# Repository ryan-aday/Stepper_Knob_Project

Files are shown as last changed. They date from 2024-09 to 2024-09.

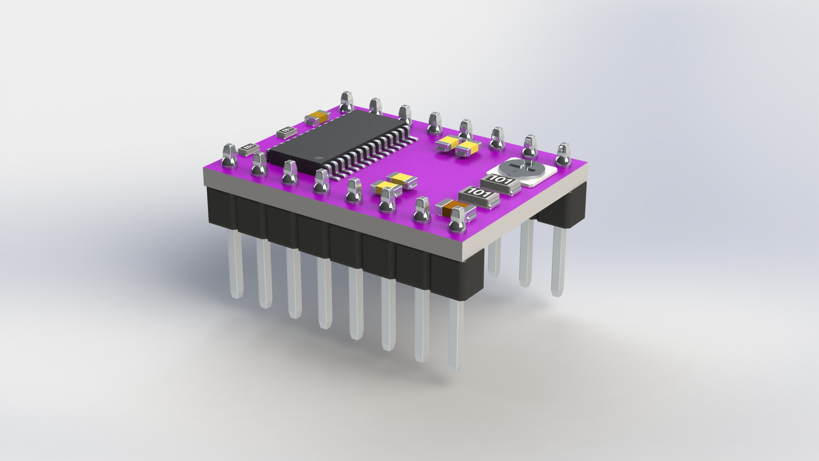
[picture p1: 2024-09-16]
Assem_PCB_Mockup/stepper-motor-driver-drv8825-1.snapshot.2/Stepper Motor Driver DRV8825 3DView.JPG

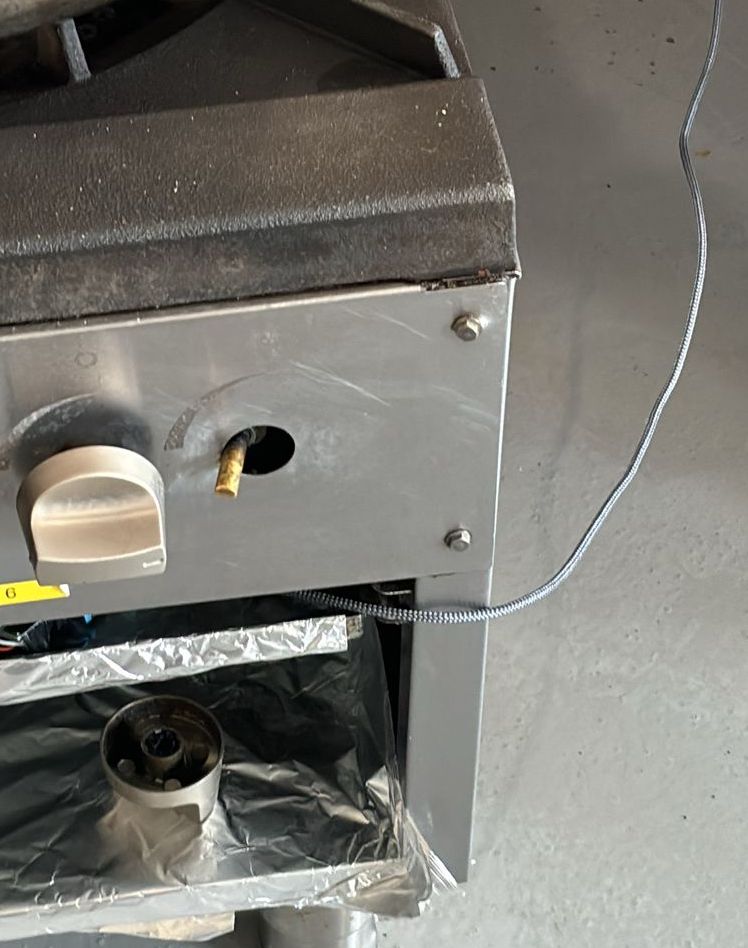
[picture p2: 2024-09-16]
Documentation/SampleGasKnobs/SampleGasKnobs/SlantedPin.jpg

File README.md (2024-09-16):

# Stepper_Knob
Hardware, firmware development of an automatable kitchen knob.



## Documentation

The CAD files have been drawn up in Solidworks 2024.

The main assembly to view is Knob_Assembly_SM.sldasm.

CAD files made by me are for the potentiometer, stepper motor, knob, and chassis.

Full size chassis drawings may be found in the Documentation folder and the Summary Sheet.

Other parts drawings may be found in the BOM references.

The summary sheet can be opened with LibreOffice and its equivalents.

The stepper schematic can be opened with Fritzing (v.1.0.3 recommended as of 09/16/2024). https://fritzing.org/

### Chassis Sheet Metal Flat Drawing


### Chassis Sheet Metal Flat Drawing


### Wiring Diagram
Wiring_Diag_Breadboard

### Wiring Schematic
Wiring_Diag_Schem

### PCB Mockup
PCB_Prototype

### BOM
See Documentation -> Summary Sheet -> BOM.
Total material cost is ~$150.29 sans shipping, wiring, and manufacturing costs.

| Part | Description | Vendor | Number | Unit Price | Total Cost | Link(s) |
|:---|:---|:---|---:|:---|:---|:---|
| HT17-222_RevD | Double Sided Double Pole 0.9 Deg Step Stepper Motor | Applied Motion Products | 1 | $56.00 | $56.00 | https://applied-motion.s3.amazonaws.com/documents/2D-Drawing/HT17-222_RevD.pdf https://www.applied-motion.com/s/product/step-motor-9-degreeht17222d/01t5i000000y0ElAAI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 |
| 5mm Vertical Slide Switch | Slide Switch | uxCell | 1 | $0.51 | $0.51 | https://www.amazon.com/uxcell-Vertical-Switch-Terminals-Latching/dp/B07GSJHGD2 |
| ESP32 WROOM RevE | Microcontroller | Esspressif | 1 | $10.00 | $10.00 | https://www.digikey.com/en/products/detail/espressif-systems/ESP32-DEVKITC-32E/12091810 https://www.digikey.com/en/models/9356990 https://forum.fritzing.org/t/esp32-wroom-32u/12978 https://grabcad.com/library/esp32-19 |
| 10k Ohm Through Hole Resistor  | Standard throughhole resistor | Adafruit | 1 | $0.03 | $0.03 | https://grabcad.com/library/resistors-0-5w-pitch-10-2mm-401-57mil-1 https://www.adafruit.com/product/2784 |
| DRV8833 | Stepper motor controller | Adafruit | 1 | $5.95 | $5.95 | https://www.adafruit.com/product/3297#technical-details https://github.com/adafruit/Fritzing-Library https://grabcad.com/library/stepper-motor-driver-drv8825-1 |
| 5mm Universal Joint | Universal Joint | Befenybay | 1 | $2.75 | $2.75 | https://www.amazon.com/Befenybay-Universal-Joint-Coupling-Screws/dp/B07VC9F1RH |
| RH24PC | Potentiometer | P3 America | 1 | $16.00 | $16.00 | https://p3america.com/rh24pc-110mm-series/ |
| NXFT15XH103FA2B090 | Thermistor | NXF | 1 | $0.48 | $0.48 | https://grabcad.com/library/thermistor-nxft15xh103fa2b090-1 https://www.digikey.com/en/products/detail/murata-electronics/NXFT15XH103FA2B090/5797782 |
| 9262K623 | Oil Resistant O-Ring 1mm wide 24mm ID | McMaster-Carr | 1 | $0.13 | $0.13 | https://www.mcmaster.com/9262K623/ |
| 90591A109 | Zinc-Plated Steel Nut M1.6x035mm | McMaster-Carr | 2 | $0.23 | $0.46 | https://www.mcmaster.com/90591A109/ |
| 91292A265 | 18-8 Stainless Steel Socket Head Screw M1.6x0.35 10mm long | McMaster-Carr | 2 | $0.27 | $0.53 | https://www.mcmaster.com/91292A265/ |
| 92095A119 | Button Head Hex Drive Head Screw 18-8 SS M3x0.5 15 long | McMaster-Carr | 4 | $0.06 | $0.25 | https://www.mcmaster.com/92095A119/ |
| 92095A183 | Button Head Hex Drive Screw 18-8 SS M3x0.5mm 12mm long | McMaster-Carr | 3 | $0.07 | $0.20 | https://www.mcmaster.com/92095A183/ |
| 92095A451 | Button Head Hex Drive Screw M2x0.04mm 4mm long 18-8 SS M3x0.5mm 12mm long | McMaster-Carr | 2 | $0.18 | $0.36 | https://www.mcmaster.com/92095A451/ |
| 92470A144 | Phillips Rounded Head Screw 18-8 SS No. 6 ¼” long | McMaster-Carr | 2 | $0.07 | $0.13 | https://www.mcmaster.com/92470A144/ |
| U Joint Cover | U Joint Sock (Provided Example) | McMaster-Carr | 1 | $10.00 | $10.00 | https://woodmaxx.com/product/u-joint-rubber-boot-cover/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 |
| 94000A330 | 18-8 Stainless Steel Cap Screw Nut M3x0.5mm | McMaster-Carr | 3 | $0.47 | $1.40 | https://www.mcmaster.com/94000A330/ |
| 94868A718 | Female Thread Hex Standoff 18-8 SS 4.5mm Hex 7mm Long M3x0.5mm | McMaster-Carr | 3 | $4.08 | $12.24 | https://www.mcmaster.com/94868A718/ |
| 8983K135 | SS 304 Sheet 12”x12” 0.06” thick | McMaster-Carr | 1 | $32.85 | $32.85 | https://www.mcmaster.com/8983K42/ |

### Code
See Documentation -> Stepper_Knob_Code.

This code controls a stepper motor using an ESP32, WiFi, and Bluetooth Low Energy (BLE) communication. It includes features for reading a thermistor, potentiometer, and handling motor control.
  - WiFi and BLE: It initializes WiFi and BLE to allow remote monitoring and control of the motor's position. The current potentiometer angle is transmitted via BLE notifications.
  - Stepper Motor Control: The code controls a stepper motor using a DRV8833 motor driver. It steps the motor based on the angle read from a potentiometer and allows for switching between "Free" and "Automated" modes via a toggle switch:
      - Free Mode: The motor is disabled, but the potentiometer angle is still read.
      - Automated Mode: The motor moves to match the potentiometer's position.
  - Thermistor: A thermistor is used to monitor temperature. If the temperature exceeds a set threshold (70°C), the motor is disabled to prevent thermal runaway.
  - Potentiometer: The potentiometer's analog reading is mapped to a specific angle (0 to 340 degrees) and used to control the stepper motor’s position.
  - Motor Step Calculation: The motor is stepped based on the target angle, which is calculated from the potentiometer reading. The motor control logic handles the necessary steps to rotate the motor.

This setup allows remote control and monitoring of the motor's behavior while incorporating safety measures against overheating.

### Design Philosophy Explanations
See Documentation -> Summary Sheet -> Justification.

| Feature | Description |
|---|---|
| **General Design** | Reduced volume/area taken by knob. Integrated PCB and assembly, allowing space for future proofing. |
| **Dual shaft stepper** | Less torque, but less power requirements. UL1061 wiring sufficient for 80 deg temperatures. |
| **Motor Controller** | Cheap, low voltage/power. Has built-in Wifi & BLE capability. |
| **U-Joint** | Ensures rotational accuracy, single joint for cost and space. Joint protected by a neoprene sock for chemical and heat protection. |
| **PCB Design** | Minimized hand wiring for assembly, including the switch. Used dev board for prototyping with extra ports for additional features. |
| **Thermistor** | Added for thermal runaway shutoff protection. |
| **Power** | 5V microUSB rail, also serves as a bootstrap port. Enclosed to avoid hacking, but inline with available stove source gaps. |
| **PCB Wiring** | Can be routed through a hole into the mounting space. |
| **Sheet Metal Chassis** | Cheaper for mass production, leveraging material tolerances. |
| **Sheet Metal Material & Wall Thickness** | Stainless 304 for cheap SS and corrosion resistance. Thickness calculated to be the cheapest option while avoiding ultimate strength failure (see bending_stress_calcs.py).| 
| **Sheet Metal Wall Design** | Walls angle outwards as mounting screws tighten, staying flush. Internal edges shield against contaminants and don't interfere with the stepper. |
| **Gaps** | Tolerances allow for manufacturing defects. |
| **Base Sealing for Knob** | Gasket added for chemical resistance. |
| **Buna-M O ring** | Seals against oil and contaminants, borrowed tolerance from pot. |
| **Rail Mount** | Slot designed for blockages and mounting surface spots. More self-tapping screws can be added if needed. |
| **Screws vs adhesives** | Adhesives lose shear strength over time, especially in heat. Screws offer permanent, easier cleanup. |

### Assembly Instructions
See Documentation => Summary Sheet -> Assembly with the steps w/ pictures.

**Note**: All bolts should be hand-tight to avoid stripping, with the exception of the sheet metal screws.

#### General Assembly Requirements:
- **Fastening**: You may need to solder the thermistor onto the PCB. The PCB should have plug-and-play connections for the factory stepper and potentiometer connectors.
- **Estimated Assembly Time**: 15-30 minutes max.

#### Steps:

1. **Screw standoffs** to the PCB with the 3 12mm long hex button screws.
   
2. **Mount the PCB** with the standoffs in place along the 3 holes on the sheet metal chassis. Secure with the 3 corresponding 3mm cap screws.
   
3. **Mount the vertical switch** with the 2mm bolts. The switch already has threads, so tighten until the switch is secure.
   
4. **Slide the U-joint sock** over the U-joint.
   
5. **Connect and mount one of the U-joint holes** to the shorter shaft of the stepper motor (should be the 15mm long end, where there is no raise from the base of the stepper motor). Secure the set screws.
   
6. **Add the 2 1.6mm socket head bolts** to the potentiometer such that the head of the bolt is placed at the back face of the potentiometer (where the tabs of the potentiometer fillet from). These bolts should be fed through the holes, NOT THE SLOTS, of the potentiometer.
   
7. **Push in the potentiometer** onto the other side of the stepper motor (long shaft side) such that the back face of the potentiometer (where the socket screw head should be) is as close to the stepper motor base as possible. The shaft of the stepper motor should be 5mm OD, which is identical to the maximum distance from the chord of the potentiometer. The material of the potentiometer hole is also brass, so a press fit is possible.
   
8. **Add the O-ring** on the ridge of the potentiometer.
   
9. **Mount the stepper motor/potentiometer** on the sheet metal chassis such that the universal joint is facing towards the open end of the chassis.
   
10. **Secure the stepper motor/potentiometer** with the 4 M3x0.5, 15mm long bolts and the 2 M1.6 nuts.
    
11. **Connect all electrical connections** to the PCB (stepper motor, primarily). This assumes the switch and thermistor are already connected to the PCB. For the thermistor, tape the ends to a wall onto the chassis and solder the leads onto the PCB.
    
12. **Ensure that the top of the chassis** is aligned with the top of the stove. You should see the open slotted chassis tab towards the top and the words “Free” and “Auto” displayed horizontally.
    
13. **Route the USB cable** from the stove and connect it to the microcontroller to provide power.
    
14. **Mount the universal joint end** to the stove shaft, and tighten the corresponding set screw.
    
15. **Screw into the mounting surface** with the self-tapping screws. Stop screwing the screws after you notice the top and bottom tabs to be flush against the mounting surface.
    
16. **Mount the knob** onto the exposed shaft by pushing it in. This should be a tight press fit.

### Prototype to Manufacturing

#### Timeline:
**1 month for prototyping & testing, 1-2 months for manufacturing 200 units**.
*(may take longer depending on shipment times)*

1. **Test for corrosion/water leaks from design.** Can do this by spraying oil, water for leak test, acetic acid for corrosion test.
   
2. **Resize microcontroller for fewer pins** if there is no future plan for adding more capabilities; consider using a tiny ASIC.
   
3. **Critical dimension check** for the length of the chassis.
   
4. **Streamline vendors** for hardware/electronic components.
   
5. **Resize PCB.** Initially wanted to keep the number of layers to 1 for ease of repair and manufacturability, but if space becomes a higher priority then to be considered.
   
6. **Consider sheet metal thickness.** There may be cheaper stainless steel sheets with thicknesses sufficient to allow for the “borrowed toleranced” side walls to flex as the mounting screws tighten. Can be calculated with cantilevered beam analysis for maximum deflection (currently 5mm).
   
7. **Use of component connectors** whenever possible to avoid additional manufacturing labor.
   
8. **Use fewer components if possible.**  Depending on space constraints, this is not always doable.

## Additional References

| Topic | Link |
|---|---|
| Fastener Conversion | [https://docs.clearpathrobotics.com/docs/robots/common/components/fasteners/screw_round_head/](https://docs.clearpathrobotics.com/docs/robots/common/components/fasteners/screw_round_head/)  |
| Stepper Motors with Arduino | [https://dronebotworkshop.com/stepper-motors-with-arduino/](https://dronebotworkshop.com/stepper-motors-with-arduino/) |
| Arduino Thermistor | [https://www.electronicwings.com/arduino/thermistor-interfacing-with-arduino-uno](https://www.electronicwings.com/arduino/thermistor-interfacing-with-arduino-uno) |
| Arduino Pot | [https://docs.arduino.cc/learn/electronics/potentiometer-basics/](https://docs.arduino.cc/learn/electronics/potentiometer-basics/) |
| 1.6 mm PCB Thickness Standard | [https://www.wevolver.com/article/pcbs-thickness-understanding-thickness-variations](https://www.wevolver.com/article/pcbs-thickness-understanding-thickness-variations) |
| UL1007 wire temp range of up to 80 deg C | [https://www.awcwire.com/allied-university/informatic/ul-1007-dual-ratings](https://www.awcwire.com/allied-university/informatic/ul-1007-dual-ratings) |
| UL1061 wire temp up to 80 deg C | [https://www.pololu.com/file/0J611/SS242x.pdf](https://www.pololu.com/file/0J611/SS242x.pdf) |
| Bending Stress | [https://smalltridesign.com/Trimaran-Articles/Stress-calcs.html](https://smalltridesign.com/Trimaran-Articles/Stress-calcs.html) |
| SS 304 | [https://www.matweb.com/search/DataSheet.aspx?MatGUID=4b43bf1211e84673bae1b2b81c7a2c01](https://www.matweb.com/search/DataSheet.aspx?MatGUID=4b43bf1211e84673bae1b2b81c7a2c01) |

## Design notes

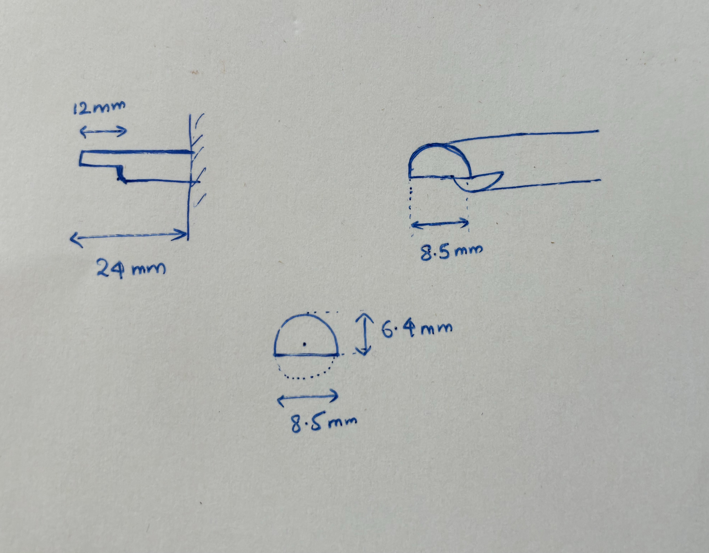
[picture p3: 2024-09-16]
Documentation/SampleGasKnobs/SampleGasKnobs/Dimensions.jpg

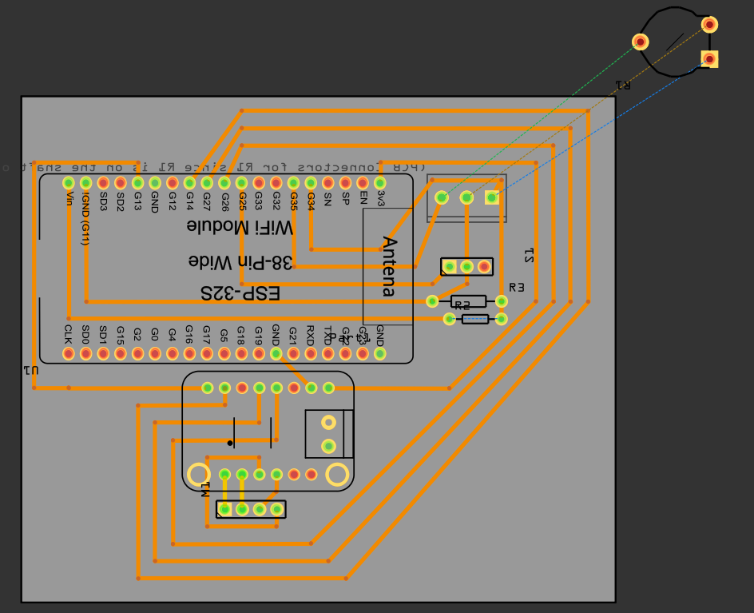
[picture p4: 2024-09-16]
Documentation/PCB_Prototype.png

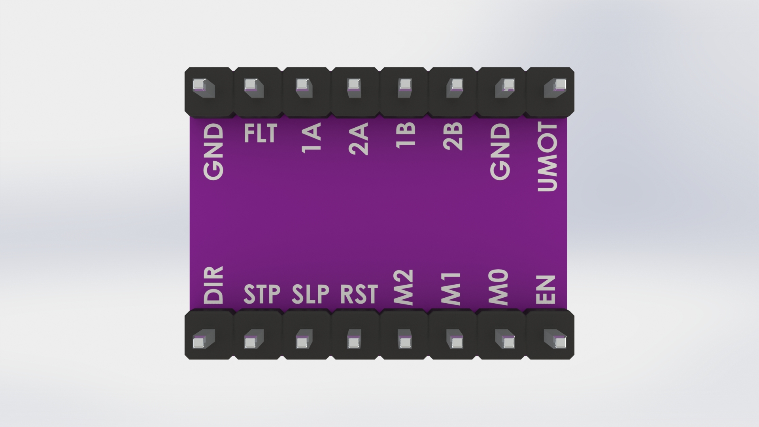
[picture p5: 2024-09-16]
Assem_PCB_Mockup/stepper-motor-driver-drv8825-1.snapshot.2/Stepper Motor Driver DRV8825 BottomView.JPG

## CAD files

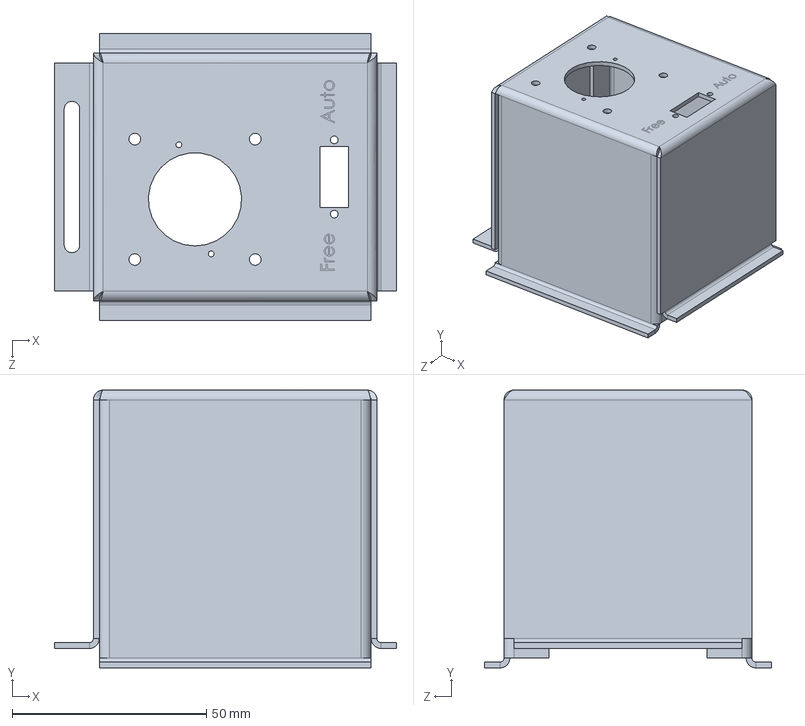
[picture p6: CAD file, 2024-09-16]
Main_Housing_SM.SLDPRT
88.0 x 71.5 x 73.8 mm

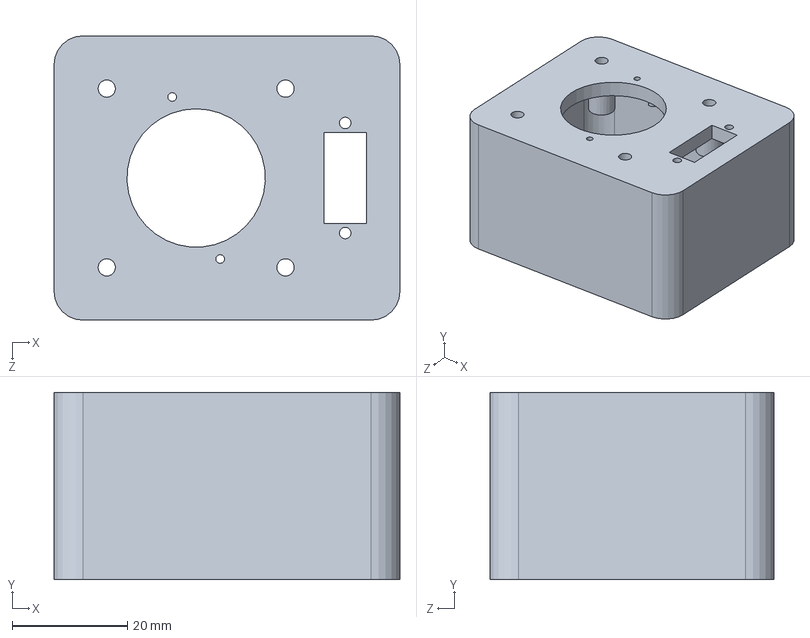
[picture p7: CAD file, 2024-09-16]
Main_Housing.SLDPRT
60.0 x 32.5 x 49.3 mm

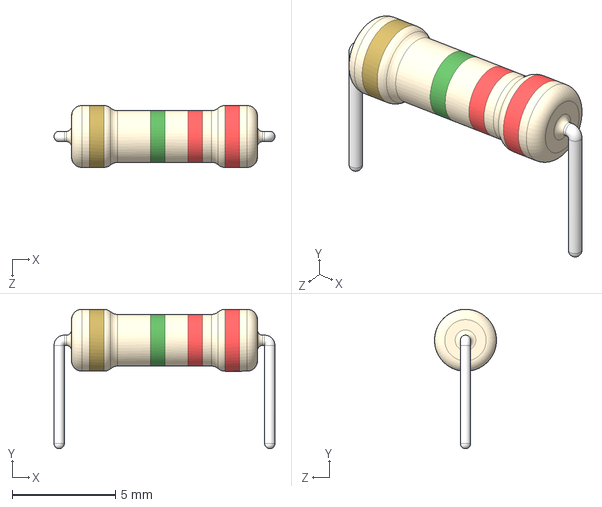
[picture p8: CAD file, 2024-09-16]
Assem_PCB_Mockup/resistors-0-5w-pitch-10-2mm-401-57mil-1.snapshot.13/Resistor Axial 0.5W - Pitch 10.2mm (401.57mil) - 2M2.STEP
10.7 x 6.75 x 3.00 mm

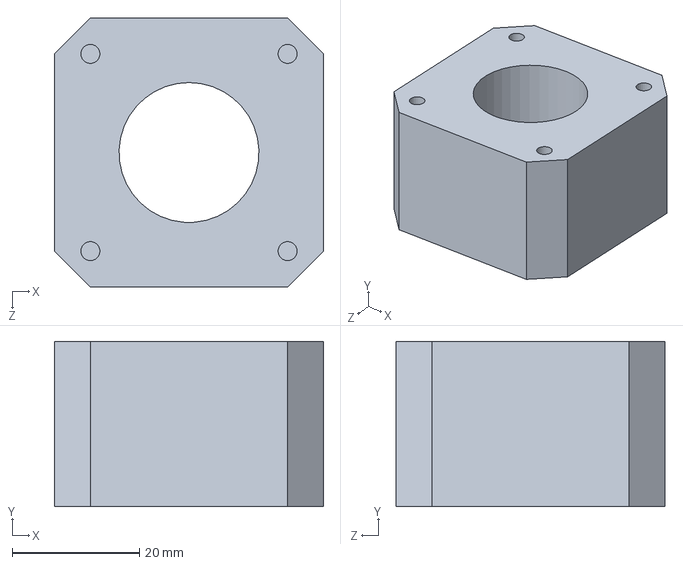
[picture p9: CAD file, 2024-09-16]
NEMA_17_Base.SLDPRT
42.3 x 26.0 x 42.3 mm

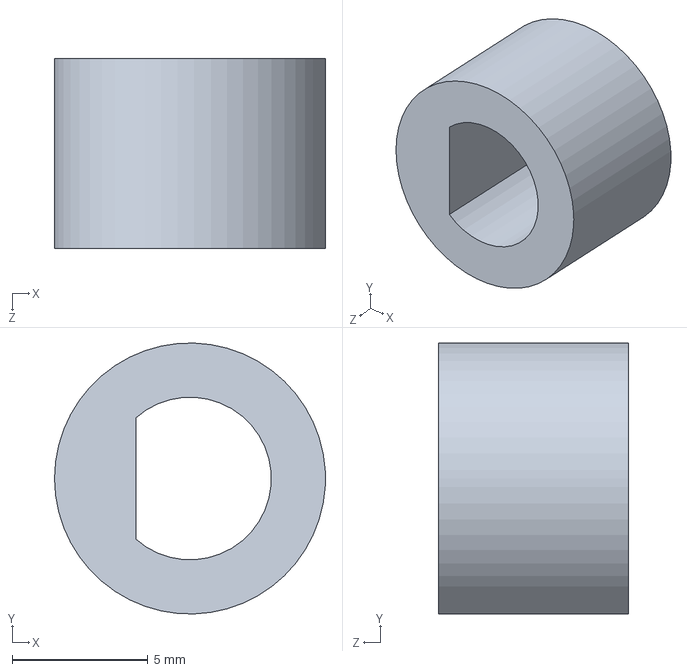
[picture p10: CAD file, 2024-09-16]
RH24PC_Pot_Shaft.SLDPRT
10.0 x 10.00 x 7.00 mm

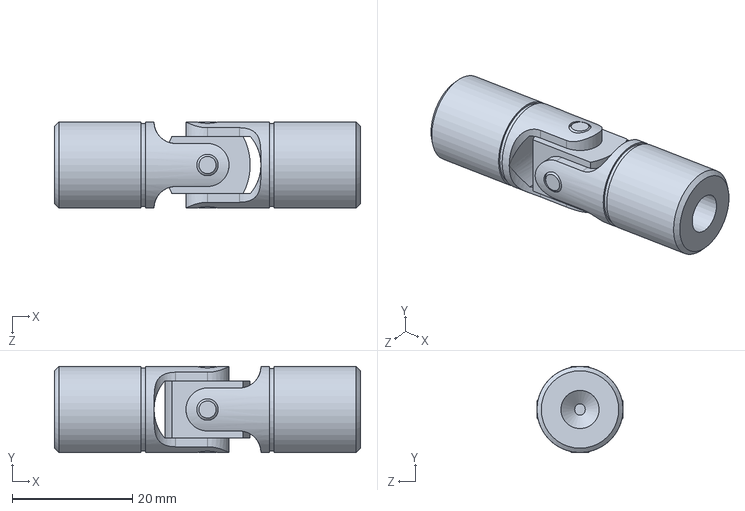
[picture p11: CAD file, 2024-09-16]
6445K1_Single U-Joint.SLDPRT
50.8 x 14.3 x 14.3 mm

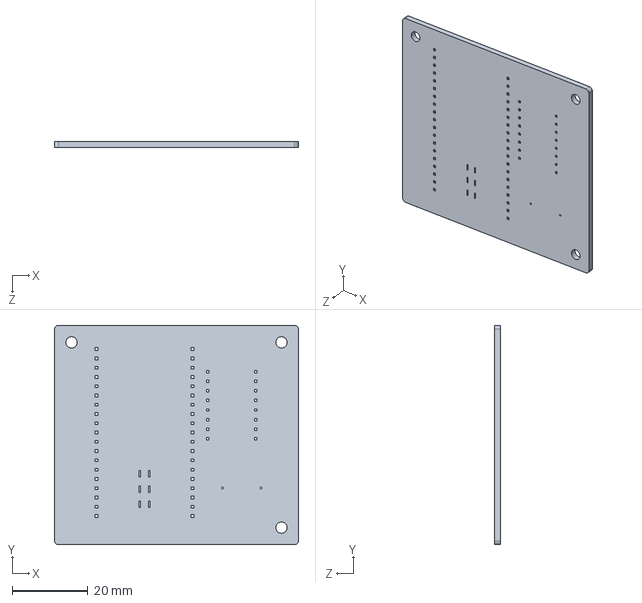
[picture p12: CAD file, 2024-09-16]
Assem_PCB_Mockup/PCB_Base.SLDPRT
64.5 x 58.0 x 1.60 mm

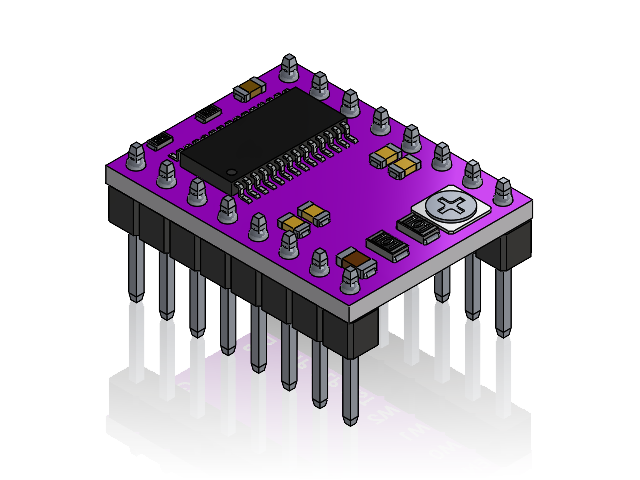
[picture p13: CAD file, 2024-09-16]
Assem_PCB_Mockup/DRV8825.SLDASM
Stepper Motor Driver DRV8825
headerMale x 16
solder x 16
tiny28pinChip
tinySMDResistor103
tinySMDResistor152
1.7mmSmdCeramicCapacitorbrown
1.7mmSmdCeramicCapacitor x 4
smdceramiccapacitorbrown
smdResistor101 x 2
TINYtRIMMER

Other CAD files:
Assem_PCB_Mockup/stepper-motor-driver-drv8825-1.snapshot.2/headerMale.SLDPRT
Assem_PCB_Mockup/Resistor Axial 0.5W - Pitch 10.2mm (401.57mil) - 10K.STEP
Assem_PCB_Mockup/resistors-0-5w-pitch-10-2mm-401-57mil-1.snapshot.13/Resistor Axial 0.5W - Pitch 10.2mm (401.57mil) - 1R8.STEP
Assem_PCB_Mockup/stepper-motor-driver-drv8825-1.snapshot.2/1.7mmSmdCeramicCapacitorbrown.SLDPRT
Assem_PCB_Mockup/resistors-0-5w-pitch-10-2mm-401-57mil-1.snapshot.13/Resistor Axial 0.5W - Pitch 10.2mm (401.57mil) - 4M7.STEP
Assem_PCB_Mockup/stepper-motor-driver-drv8825-1.snapshot.2/1.7mmSmdCeramicCapacitor.SLDPRT
Assem_PCB_Mockup/resistors-0-5w-pitch-10-2mm-401-57mil-1.snapshot.13/Resistor Axial 0.5W - Pitch 10.2mm (401.57mil) - 6R8.STEP
Assem_PCB_Mockup/stepper-motor-driver-drv8825-1.snapshot.2/tiny28pinChip.SLDPRT
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

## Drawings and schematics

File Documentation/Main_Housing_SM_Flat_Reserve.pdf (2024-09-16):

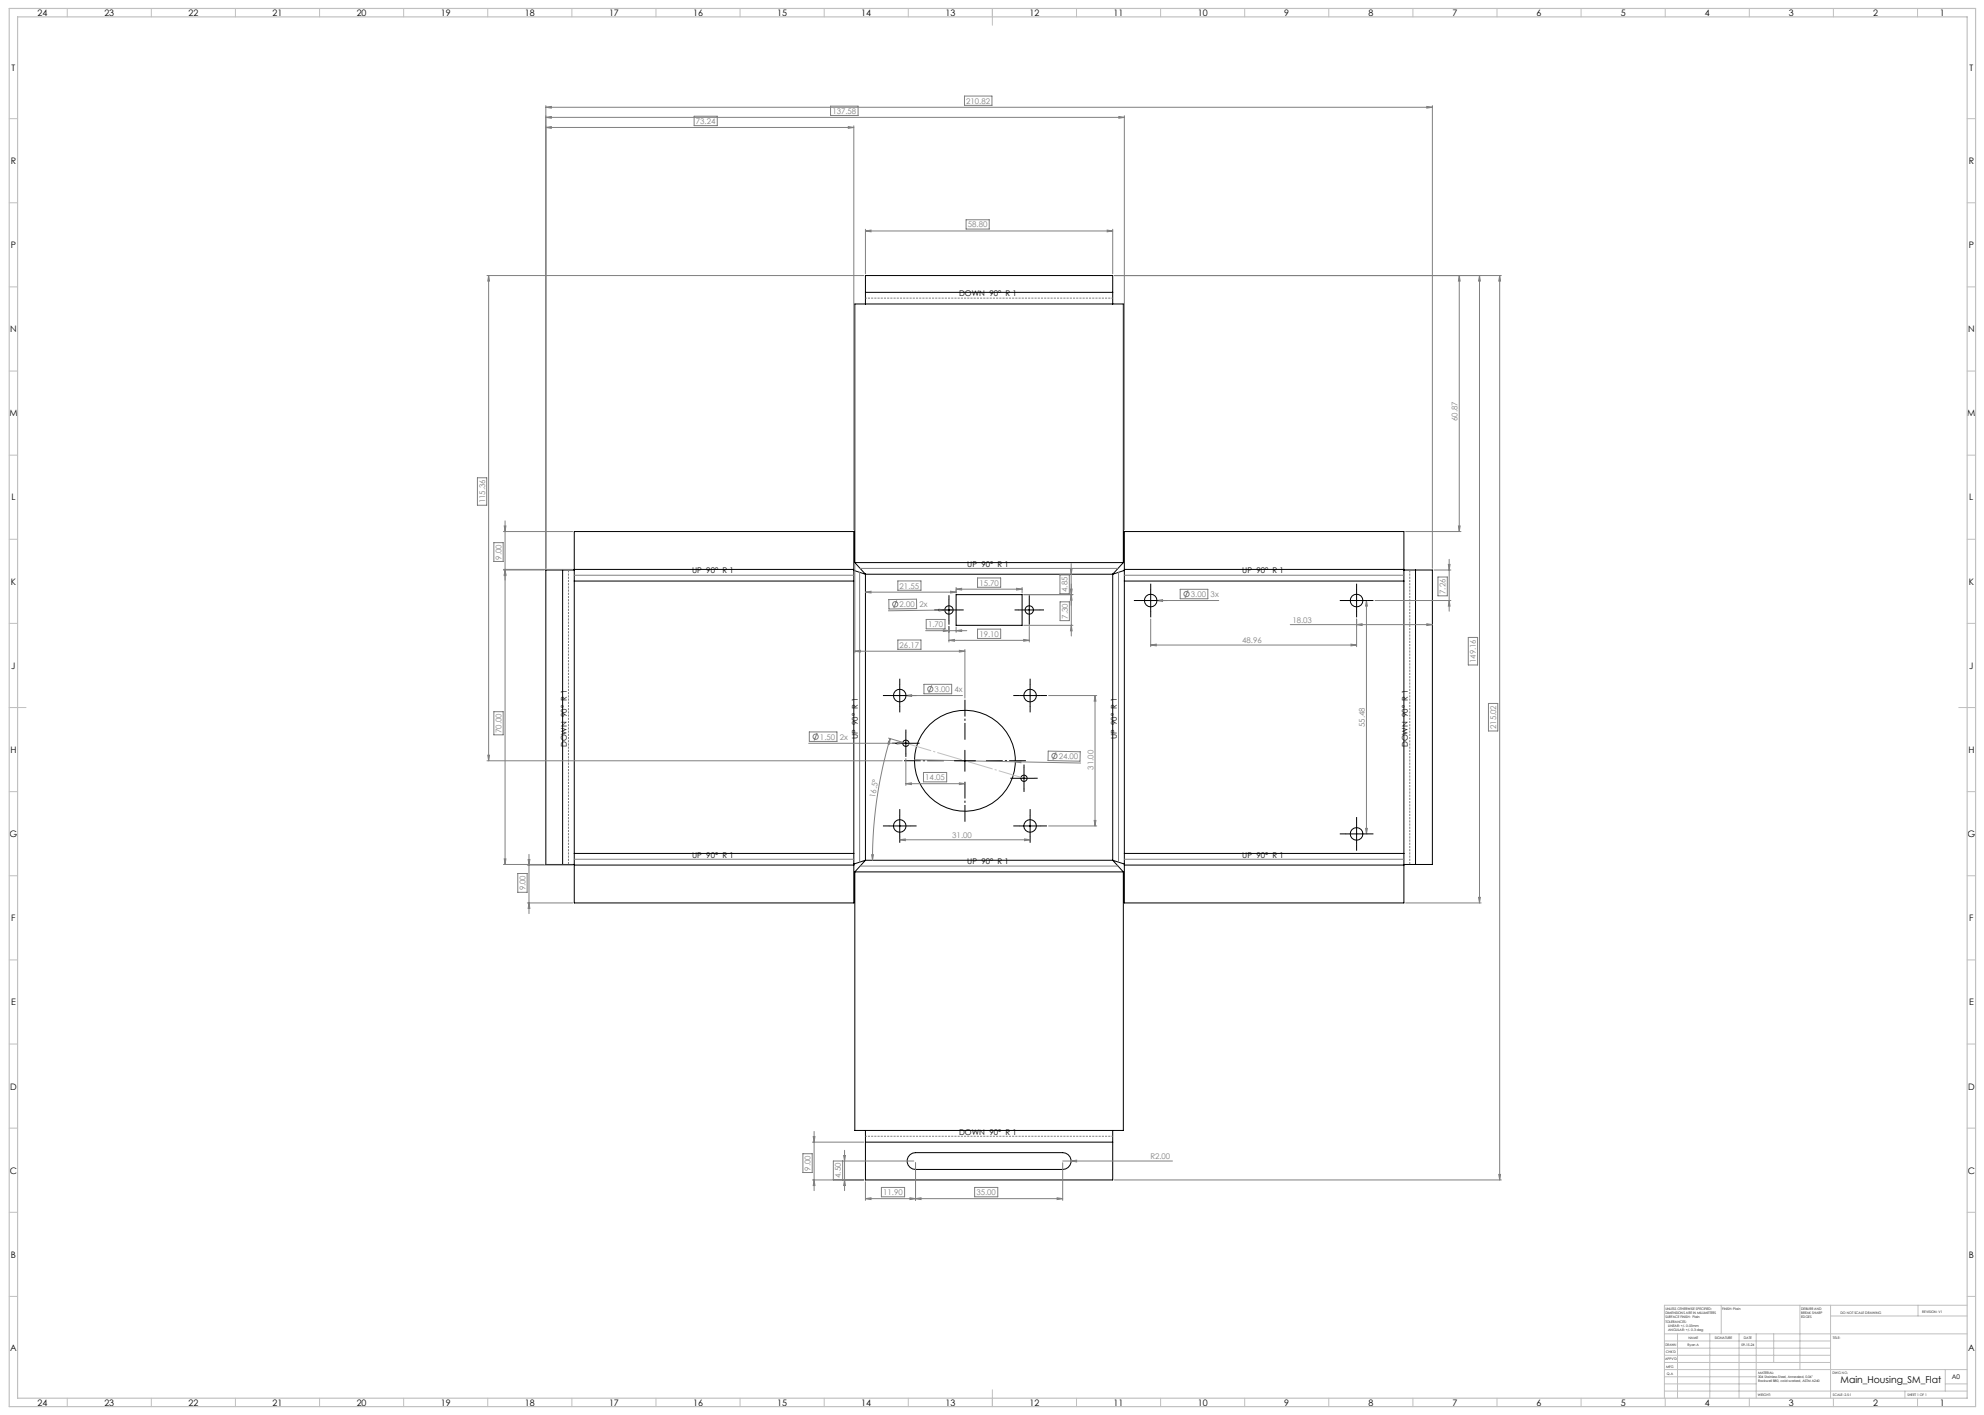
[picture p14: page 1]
DOWN 90° R 1; FINISH: Plain; DEBURR AND; BREAK SHARP; DO NOT SCALE DRAWING; REVISION: V1; SCALE: 2.5:1; SHEET 1 OF 1

UNLESS OTHERWISE SPECIFIED:
DIMENSIONS ARE IN MILLIMETERS
SURFACE FINISH: Plain
TOLERANCES:
LINEAR: +/- 0.03mm
ANGULAR: +/- 0.3 deg

NAME | SIGNATURE | DATE | | | | TITLE:

DRAWN | Ryan A | | 09-15-24
CHK'D
APPV'D
MFG
Q.A | | | | MATERIAL: 304 Stainless Steel, Annealed, 0.06" Rockwell B80, cold worked, ASTM A240 | DWG NO. Main_Housing_SM_Flat | A0

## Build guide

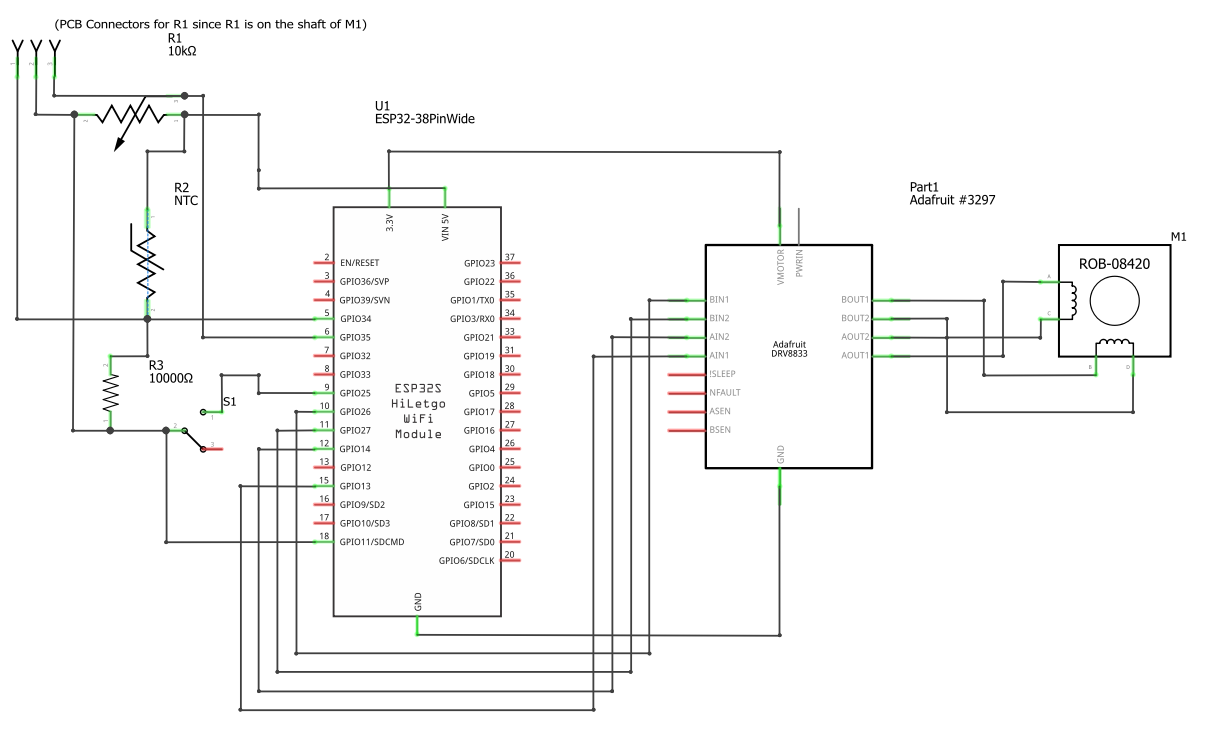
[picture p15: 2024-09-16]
Documentation/Wiring_Diag_Schem.png

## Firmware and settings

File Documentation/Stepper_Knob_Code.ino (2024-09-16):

#include <WiFi.h>
#include <BLEDevice.h>
#include <BLEServer.h>
#include <BLEUtils.h>
#include <BLE2902.h>

// Pin Definitions for DRV8833 (Motor control pins)
#define MOTOR_IN1 13   // Stepper motor winding A+
#define MOTOR_IN2 14   // Stepper motor winding A-
#define MOTOR_IN3 27   // Stepper motor winding B+
#define MOTOR_IN4 26   // Stepper motor winding B-
#define ENABLE_PIN 12  // Enable/Disable motor (to simulate power cut)
#define TOGGLE_PIN 25  // Pin for the toggle switch (Free/Automated mode)
#define THERMISTOR_PIN 34  // Analog pin for the thermistor
#define POTENTIOMETER_PIN 35  // Analog pin for the potentiometer

// WiFi Credentials
const char *ssid = "yourSSID";
const char *password = "yourPASSWORD";

// BLE Service UUID
BLEServer *bleServer;
BLEService *bleService;
BLECharacteristic *bleChar;
const char *bleServiceUUID = "0000180A-0000-1000-8000-00805F9B34FB";
const char *bleCharUUID = "00002A29-0000-1000-8000-00805F9B34FB";

// Thermistor Parameters
#define NOMINAL_RESISTANCE 10000    // Resistance at 25 degrees Celsius
#define NOMINAL_TEMPERATURE 25      // Temperature for nominal resistance (Celsius)
#define B_COEFFICIENT 3950          // Beta coefficient of the thermistor
#define SERIES_RESISTOR 10000       // Value of the series resistor

// Potentiometer Configuration (RH24PC Potentiometer)
#define POT_MIN_ANGLE 0             // Min angle of potentiometer
#define POT_MAX_ANGLE 340           // Max angle of potentiometer (340° as per specs)
#define ADC_MAX_VALUE 4095          // 12-bit ADC on ESP32

// Stepper Motor Configurations
#define STEPS_PER_REV 400           // 0.9° per step (360 / 0.9 = 400)
#define MICROSTEP_MODE 1            // No microstepping in DRV8833 (full step control)
#define STEP_DELAY 2                // Delay between steps in milliseconds

// Thermal Runaway Threshold
#define MAX_TEMP_CELSIUS 70.0

// Function to read temperature from the thermistor
float readThermistor() {
  int analogValue = analogRead(THERMISTOR_PIN);
  float resistance = SERIES_RESISTOR / ((4096.0 / analogValue) - 1);
  float steinhart;
  steinhart = resistance / NOMINAL_RESISTANCE;           // (R/Ro)
  steinhart = log(steinhart);                            // ln(R/Ro)
  steinhart /= B_COEFFICIENT;                            // 1/B * ln(R/Ro)
  steinhart += 1.0 / (NOMINAL_TEMPERATURE + 273.15);     // + (1/To)
  steinhart = 1.0 / steinhart;                           // Invert
  steinhart -= 273.15;                                   // Convert to Celsius
  return steinhart;
}

// Function to prevent thermal runaway
void thermalRunawayPrevention() {
  float temperature = readThermistor();
  if (temperature > MAX_TEMP_CELSIUS) {
    Serial.println("Warning: Thermal Runaway Detected! Shutting down motor.");
    digitalWrite(ENABLE_PIN, HIGH);  // Disable stepper motor (cut power)
  } else {
    digitalWrite(ENABLE_PIN, LOW);   // Enable motor if temperature is within safe limits
  }
}

// Function to initialize BLE
void initBLE() {
  BLEDevice::init("MotorizedKnob");
  bleServer = BLEDevice::createServer();
  bleService = bleServer->createService(bleServiceUUID);
  
  bleChar = bleService->createCharacteristic(
               bleCharUUID,
               BLECharacteristic::PROPERTY_READ |
               BLECharacteristic::PROPERTY_NOTIFY
             );
  bleService->start();
  BLEDevice::startAdvertising();
  Serial.println("BLE Initialized.");
}

// Function to connect to WiFi
void initWiFi() {
  WiFi.begin(ssid, password);
  while (WiFi.status() != WL_CONNECTED) {
    delay(1000);
    Serial.println("Connecting to WiFi...");
  }
  Serial.println("Connected to WiFi.");
}

// Function to read angle from potentiometer
float readPotentiometer() {
  int potValue = analogRead(POTENTIOMETER_PIN);  // Read the potentiometer's analog value
  float angle = map(potValue, 0, ADC_MAX_VALUE, POT_MIN_ANGLE, POT_MAX_ANGLE);  // Map the potentiometer reading to an angle (0-340 degrees)
  Serial.print("Current Angle: ");
  Serial.println(angle);
  return angle;
}

// Function to move the stepper motor by one step (DRV8833 H-Bridge control)
void stepMotor(int step) {
  switch (step % 4) {
    case 0:
      digitalWrite(MOTOR_IN1, HIGH);
      digitalWrite(MOTOR_IN2, LOW);
      digitalWrite(MOTOR_IN3, HIGH);
      digitalWrite(MOTOR_IN4, LOW);
      break;
    case 1:
      digitalWrite(MOTOR_IN1, LOW);
      digitalWrite(MOTOR_IN2, HIGH);
      digitalWrite(MOTOR_IN3, HIGH);
      digitalWrite(MOTOR_IN4, LOW);
      break;
    case 2:
      digitalWrite(MOTOR_IN1, LOW);
      digitalWrite(MOTOR_IN2, HIGH);
      digitalWrite(MOTOR_IN3, LOW);
      digitalWrite(MOTOR_IN4, HIGH);
      break;
    case 3:
      digitalWrite(MOTOR_IN1, HIGH);
      digitalWrite(MOTOR_IN2, LOW);
      digitalWrite(MOTOR_IN3, LOW);
      digitalWrite(MOTOR_IN4, HIGH);
      break;
  }
  delay(STEP_DELAY);
}

// Function to move stepper motor to a specific angle
void moveStepperToAngle(float targetAngle) {
  int steps = (targetAngle / 360.0) * (STEPS_PER_REV * MICROSTEP_MODE);
  for (int i = 0; i < steps; i++) {
    stepMotor(i);
  }
}

// Function to handle Free and Automated mode toggle
void handleToggleSwitch() {
  int toggleState = digitalRead(TOGGLE_PIN);

  if (toggleState == HIGH) {
    // Free Mode: Disable the motor but still read the knob angle
    Serial.println("Free Mode Activated");
    digitalWrite(ENABLE_PIN, HIGH);  // Disable stepper motor (cut power)
  } else {
    // Automated Mode: Enable the motor and control the angle
    Serial.println("Automated Mode Activated");
    digitalWrite(ENABLE_PIN, LOW);   // Enable stepper motor
  }
}

void setup() {
  Serial.begin(115200);

  // Initialize WiFi and BLE
  initWiFi();
  initBLE();

  // Initialize motor and toggle switch
  pinMode(MOTOR_IN1, OUTPUT);
  pinMode(MOTOR_IN2, OUTPUT);
  pinMode(MOTOR_IN3, OUTPUT);
  pinMode(MOTOR_IN4, OUTPUT);
  pinMode(ENABLE_PIN, OUTPUT);
  pinMode(TOGGLE_PIN, INPUT_PULLUP); // Toggle switch input, using pull-up resistor

  // Set the motor to disabled by default
  digitalWrite(ENABLE_PIN, HIGH);

  Serial.println("Setup completed.");
}

void loop() {
  // Read temperature and prevent thermal runaway
  thermalRunawayPrevention();

  // Read angle from potentiometer and send via BLE
  float currentAngle = readPotentiometer();
  bleChar->setValue(String(currentAngle).c_str());
  bleChar->notify();

  // Check the state of the toggle switch
  handleToggleSwitch();

  // If in automated mode, move the motor to the desired angle
  if (digitalRead(TOGGLE_PIN) == LOW) {
    moveStepperToAngle(currentAngle);  // Move the stepper motor to the current potentiometer angle
  }

  delay(1000);  // Adjust delay as needed
}
